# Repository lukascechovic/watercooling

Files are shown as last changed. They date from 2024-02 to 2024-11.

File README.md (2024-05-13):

# Watercooling for 3d printer based on Vz235 build and Mellow motor, drivers and extruder aluminium watercooling blocks. Warning page is under construction!

Experiences from building up watercooled 3d printer or how to make rigth choices for your build. Information based on internet "research" and communication with PC watercooling community, Alphacool and EKWB company info lines.

**Long story short** 

- one big loop
- D5/VPP655 (maybe Apex pump as cheaper D5 compatible variant)
- 2.4/4mm tubing (easy routing around printer)(polyurethane (10m) and optional silicone/pvc(2m) softer for printhead)
- 3x12cm aluminium radiator for easy top mounting (price 2eur more than 2x12 rad)
- brass nickel plated fittings (optional stainless steel 304)(idealy aluminium but I was not able to find any in this world) 
- clear coolant premix

##  Reasoning for this advice should be found next if you wanna dig deeper.

1. Mellow items for watercooling our 3D pritner https://github.com/lukascechovic/watercooling/tree/main/mellow_items
2. Fittings https://github.com/lukascechovic/watercooling/tree/main/fittings
3. Tubing https://github.com/lukascechovic/watercooling/tree/main/tubing
4. Loop topology https://github.com/lukascechovic/watercooling/tree/main/loop_topology
5. Macros to solve multiple states controlling same pin (pump and radiator fans) https://github.com/lukascechovic/watercooling/tree/main/macros
6. Stl files of pump, radiator, tubing mounts https://github.com/lukascechovic/watercooling/tree/main/cad_stl_files
7. Official statements from infolines EKWB and Alphacool https://github.com/lukascechovic/watercooling/tree/main/research%20info%20gathered

## Underline

1. **Why choose D5 pump?** It is PC watercooling industry standart. Even EKWB product video comparing D5 to other smaller DCC pump started with joke "just take D5". And yes, taking anything other than D5 is compromise. Pricewise there is nearly no difference as in smaller pump you pay for small form factor. Big one is that D5 is running at 24V so PC comunity cannot use full potential of this pump. But we can! 24V is our standart voltage :-) .

2. **Starting with budget Mellow watercooling kit?** If you dont wanna spend more than 70 euro just take Mellow watercooling kit and you will be happy and somehow youll find the way to ignore pump vibrations. But if we are building printer worth 2000 euros in items, are we wealthy enough to buy cheap things? Mellow water-cooling kit was 70 euro learning experience for me. I wish to be able skip that step.

3. **Price?**
 - 70 euro - Mellow watercooling kit
 - up to 160 euro - profi items ex. Alphacool D5-VPP655 set with reservoir, with 3x12 rad up to 160 euro (you can cut price with choosing Apex variant of the pump)

4. **Reservoir** - just take any size you like. With bigger one its easier to start loop. Our loop has around 300 ml of fluid with all possible blocks and 3x12 radiator so its no big deal even with smallest reservoir.

5. **Head pressure** - This parameter was harder one to evaluate as usually smaller pumps as DCC have bigger head pressure than D5 pumps. Head pressure is how the pump is able to overcome flow restrictions. But its also dependant from flow. If we watch only extremes from pump graphs the small DCC could seems better with higher head pressure than D5, but flow of the D5 is many times bigger than DCC with just small head pressure loss.
6.  **Coolant** - I got this answer on Alphacool forums "I'd recommend staying away from dyes just to be safe. I use Mystic Fog in my rig for the RGB effect but I accept the risk of clogs and higher maintenance involved." So if you wanna stay out of trouble just go for Clear coolant premix.

## TODO:
*add BOM

*add screws parameters

*Chatgpt please make this text readable

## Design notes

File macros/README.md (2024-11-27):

# *Temp_monitor.cfg macro turning on and off watercooling of 3d printer

## When you have watercooled extruder, drivers, motors it was neccessary to be able run watercooling for each state but with standard way you are not able to assign one pin to multiple objects.

## It is based on delayed macro which works as timer interrupt and run code which check activity and temperatures of drivers, motors, extruder, using dummy fans with fake nonused pins which can combine behaviour of controller and heater fan. 

## printer.cfg and leds.cfg to clarify pin assignement

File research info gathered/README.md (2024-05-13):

# Watercooling for 3d printers
Experiences from building up watercooled 3d printer or how to make rigth choices for your build. Information based on internet "research" and communication with PC watercooling community, Alphacool and EKWB company info lines.

*issue -1: Official statements from infolines*

**EKWB**

**Note:** Question about if EKWB D5/DDC pump can be used in aluminium loop, answer is **NO**

***Question 1:*** Hello, I would like to buy pupm from you into custom aluminium loop (alu blocks and radiators). I got confused with note in your products "This product should NOT be installed with any aluminum Fluid Gaming parts!" . Does it means I cannot use it in Aluminium containing loop? Could you please explaint to me that note and are your pumps suitable to work in custom all aluminium loop? Thanks. Have a nice day.

***Answer 1:*** Hello, thank you for contacting us. The mentioned product is not compatible with ALU parts. We used to sell products that were compatible with ALU products. Unfortunately, we no longer sell ALU products. We still have some ALU water blocks or fittings available. Unfortunately, radiators and water pumps are no longer available.

***Question 2:*** Can the 'EK-Classic Pump Reservoir 160 SPC PWM' be used in an aluminum loop?

***Answer 2:*** The EK-Classic Pump Reservoir 160 SPC PWM can be used in an aluminum loop but you will have to replace the nickel-plated brass plug with a plastic one.

**Alphacool**

***Question 1:*** Hello, I'm looking for pump into full alluminium loop. Its for custom machine with low diametter tubing (4 or 6 mm) in total length up to 10m, with 7 small aluminium blocks. If I'm not wrong I should look for higher head meters value pump. I'm searching for answers for several days but no luck for now. Last info I got is that I cannot use even stainless steel parts pump with aluminium. VPP655 pumps are marked as ceramic and plastic (Kunststoff;Keramik;) but on video they've definitely got some other metal inside. What pumps I can use in aluminium containing loop? Thanks for answer. Have a nice day.

***Answer 1:*** Hi Lukas, you can use all pump sin our assortment for full copper or aluminium loops. https://shop.alphacool.com/shop/pumpen/

***Question 2:*** "What type of metal fittings other than aluminium  can be used in full aluminium loops?  Stainless steel, brass, other?"

***Answer 2:*** Hi Lukas, thank you for getting back. Our fittings are all anodized, painted or nickel-plated and they have no contact with the liquid, so you can use any of our fittings in your loop.

***Question 3:*** "It is possible to use multiple outputs/inputs same time on the Alphacool Eisdecke Laing DDC Acryl top V.2 or Alphacool Eisdecke DDC Acryl top V.4? For example if I need to have/create two loops?"

***Answer 3:*** Hi Lukas, I am sorry but it isn´t possible to use multiple Outs on the products. **It isn´t also recommended to make a parallel loop. If you want two different loops, you will need two pumps and reservoirs.
**

**Alphacool Forums**

***Question 1:*** Hello guys,

looking for advices to optimize watercooling build for 3d printer and choose rigth components.

Setting:
-> 500wats TDP max
-> Aluminium cooling blocks on components
-> M5 and M6 threads on aluminium blocks = fittings only for 4/2.5 and 6/4 mm tubing (OD/ID) (one moving component (printihead) needs to stay on 4/2.5 tubing due to moving restrictions and weigth)
-> length of tubing max 10meters (7 components around the machine)
-> difference between highest and lowest point on machine is 0.5m
-> No hard space restrictions for radiator and pump (but more compact and visually pleasing solution is preffered)
-> prefered silent (low/no vibration operation)

Concerns:
-> choosing rigth pump for length of the loop and tubing diametters
-> choosing big enough radiator for the TDP (aluminium one due to alu blocks on components)
-> topogy of the cooling (atleast two loops ? - one for 4/2.5 tubing and one for 6/4 tubing)

So far I was thinking about:
Radiator: Alphacool ES Aluminium 360 mm T27
Fans: Yate Loon D12SH-12 with plug (2200rpm) ( 120x120x25mm )
Pump: ??
Topology: two loops

Thanks for ideas!!

PS: Some alphacool water pumps have this statement in description "Please use only in conjunction with clear transparent water cooling fluids. The particles and additives in Pastel liquids can clog and permanently damage water cooling products such as radiators, pumps, coolers and hoses.". I cant use any color premixed collants with this items or it is some special kind of colored coolants liquids and apply only for "pastels ones"?

***Answer 1:*** 1 D5 pump should be all you need unless you are doing discrete loops. If you are cooling multiple components you don't need multiple loops. Just run it in series and you'll be fine and save some money and headaches. I'd recommend staying away from dyes just to be safe. I use Mystic Fog in my rig for the RGB effect but I accept the risk of clogs and higher maintenance involved. That rad should work fine for 500 watts. Those fans should be fine also.
Edit: Just use this coolant for the best performance and longevity of the loop.

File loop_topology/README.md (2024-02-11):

# *Starting point "...just run it in series and you'll be fine and save some money and headaches."*
*PC watercooling practise*

1. You dont need high flow
2. One loop
3. Order of items in loop is not important
4. Radiator is main player in capacity of the loop to disipate heat

Explanation:

https://github.com/lukascechovic/watercooling/tree/main/research%20info%20gathered

1. You dont need high flow = lower flow = more time in radiator = lower temperature of coolant at radiator output
2. One loop = "If you are cooling multiple components you don't need multiple loops. Just run it in series and you'll be fine and save some money and headaches." I got simmilar responces from PC watercooling comunity, you can found them also beneath Vez3D videos on this topic.
3. Order of items in loop is not important = you can find lots of video on Youtube for example @Jayztwocents "Watercooling Loop Order... Does it REALLY matter?? Here's Proof" https://www.youtube.com/watch?v=RnPB_q51iVk&t=130s
4. Radiator is main player in capacity of the loop to disipate heat. And as there is a little price difference between 1x12, 2x12, 3x12 radiators. There is no good reason to not take 3x12 as futureproof choice for your build. You can have 3x12 rad from renowed brand for as little as 32 eur. Bigger radiator is easier to mount on the top of the build and also cool whole electronics.
   
   For example aluminium radiators https://shop.alphacool.com/en/shop/radiators/industrial-radiators/

*Note: My watercooling journey started on Vez3D youtube channel https://www.youtube.com/@Vez3D*

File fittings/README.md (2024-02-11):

# *Starting point*

1. aluminium cooling blocks from Mellow with M5 and M6 (driver block) threads and 4mm OD tubing
2. to preventing galvanic corrosion we should use all items with same metal as mellow blocks = aluminium

## Fittings material

***Conclusion:** my searching for full aluminium fittings failed. Closest I got were items from https://tameson.com/collections/aluminum-push-on-fittings . But upod delivery I realised that item description is false and they contain steel parts. So based on Alphacool statement we should be fine with nickel plated brass fittings with premix coolant water*

We can easily buy brass and copper nickel plated fittings and stainless steel 304 fittings, but in theory neither of those should be used together with aluminium in one cooling loop.

Here is EKWB blog on this topic with lot of details https://www.ekwb.com/blog/aluminium-vs-copper/

EKWB as main player in PC watercooling is strct about this, they are even prohibiting to use their pumps in aluminium containing loops.

On the other hand Alphacool as other player in this alows use all of their pumps in aluminium and copper loops and also using their brass nickel plated fittings in aluminium loops. (https://github.com/lukascechovic/watercooling/tree/main/research%20info%20gathered). But to be fair their statement "Our fittings are all anodized, painted or nickel-plated and they have no contact with the liquid, so you can use any of our fittings in your loop." sounds little weird to me.

EKWB picture
Galvanic_corrosion

Note to the stainless steel, in our conditions should be active if I understand it well.
active_passive_steel

## Fitting diameters

*So we have to use M5 and M6 sized fitting to fit into Mellow blocks. Inner diametter of M5 sized fitting is aproximatelly 1.8mm independent from tubing connection 2.5mm or 4mm ID. So there is questionable need for 4/6mm tubing as there is up 12 fittings with M5 screws with 1.78mm opening. To have complete info M5-4mm OD fitting have 1.66mm hole on tubing side.*

obrázok

## Fitting type
Push on compresion fittings looks like best option however even push in plastic ones, which you get with Mellow blocks, works fine for all types of tubing. Concerns with plastic ones could be heated chamber and higher temperatures.

Example of fittings:

https://www.aliexpress.com/item/1005003562742686.html?spm=a2g0o.cart.0.0.8af938davIDzIX&mp=1

https://www.aliexpress.com/item/1005001971376554.html?spm=a2g0o.cart.0.0.67b838daCjOm6Y&mp=1

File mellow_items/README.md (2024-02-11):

# *Mellow watercooling items for 3d printers

## Mellow complete basic watercooling kit

*Comment:* *Cheap and complete set, everything you need to start. Concerns are low quality controll and pump with lots of vibrations (compare to D5/DCC pumps). If you think you can somehow isolate those vibrations while pump stays on printer, you most probably dont, atleast I wasnt succesfull."

https://www.aliexpress.com/item/32888175838.html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

## Motor blocks for nema17 - included elbow fittings M5 - 4mm OD !! screws just for one length of motors

https://www.aliexpress.com/item/1005005773478512.html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,scm-url:1007.40000.327270.0,pvid:dc4a4057-3f06-441a-ac3a-f96fc6f4c963,tpp_buckets:668%232846%238115%232000&pdp_npi=4%40dis%21EUR%2136.55%2129.24%21%21%2138.47%2130.78%21%402101cff817076547497267387ee921%2112000034301466627%21rec%21SK%211841669886%21&utparam-url=scene%3ApcDetailTopMoreOtherSeller%7Cquery_from%3A

## Drivers 5160 Mellow Fly pro blocks - included M6 - 4mm OD elbow fittings

https://www.aliexpress.com/item/1005006244492970.html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,scm-url:1007.40000.327270.0,pvid:47da6230-7e59-4bf5-be31-37e7c4645041,tpp_buckets:668%232846%238115%232000&pdp_npi=4%40dis%21EUR%2161.41%2152.20%21%21%2164.63%2154.94%21%402101cff817076547551617470ee921%2112000036445101785%21rec%21SK%211841669886%21&utparam-url=scene%3ApcDetailTopMoreOtherSeller%7Cquery_from%3A

## Vz-Hextrudort-Low/WC Extruder - included M5 - 4mm OD elbow fittings

https://www.aliexpress.com/item/1005004574888848.html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

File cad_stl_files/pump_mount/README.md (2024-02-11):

# Mount for Alphacool Core 100 Aurora reservoir in bundle with pump has great value 

## https://shop.alphacool.com/en/shop/reservoirs-distro-plates/reservoir-with-pump/15483-alphacool-core-100-aurora-d5/vpp-reservoir-acetal/acrylic-with-vpp655-pwm-pump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 (there is also cheaper version https://shop.alphacool.com/en/shop/reservoirs-distro-plates/reservoir-with-pump/15380-alphacool-core-100-aurora-reservoir-acetal/acryl-with-apex-pump)

## using alphacool decoupling set with 3d printed spacers to mount into PSU https://shop.alphacool.com/en/shop/pumpen/accessories/13701-alphacool-decoupling-set-for-eheim/hydor/laing-attachment-1xig/1xag-4-pieces

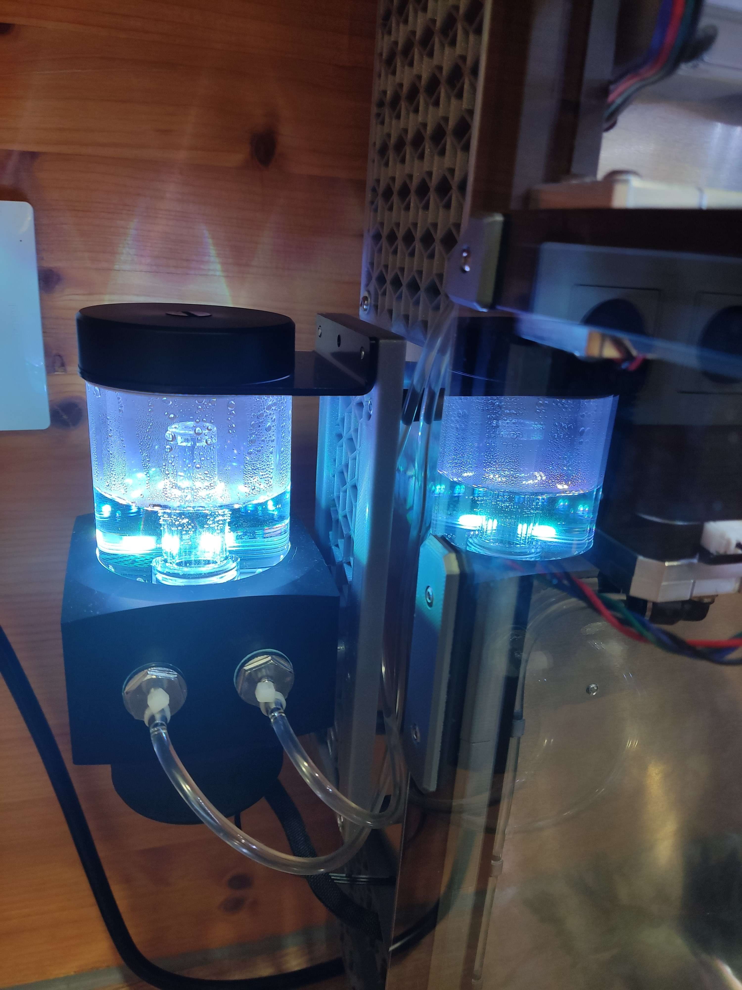
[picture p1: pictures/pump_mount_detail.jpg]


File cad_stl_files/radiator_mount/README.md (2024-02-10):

# 3x12cmm radiator top mount should work for any 3x12 radiator

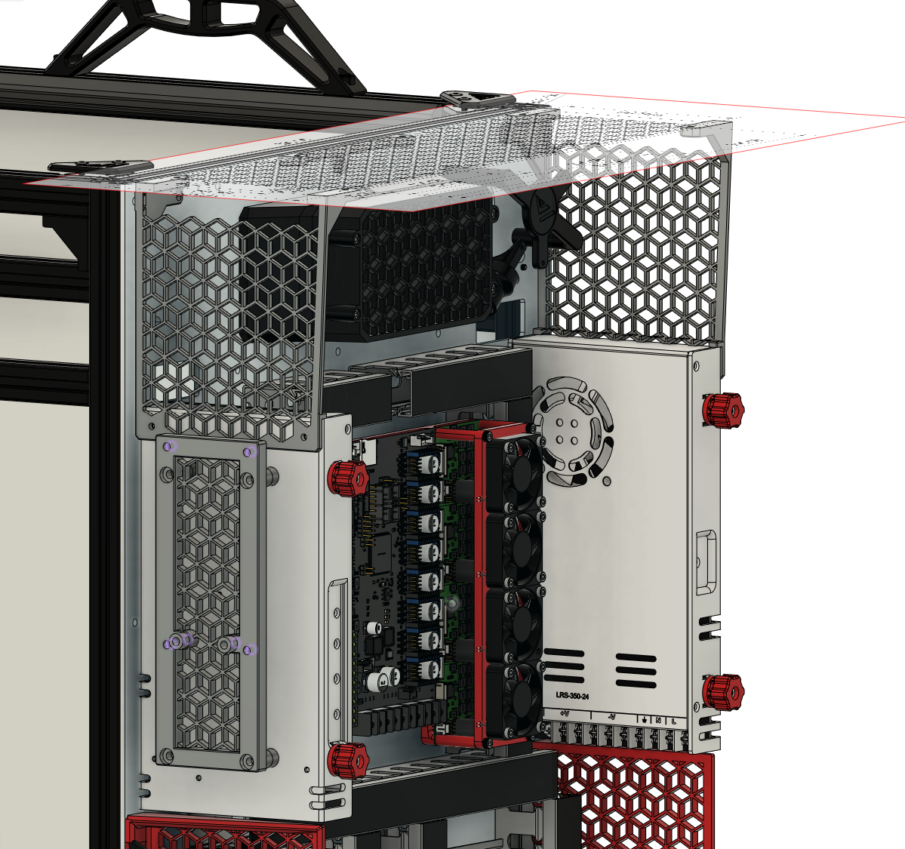
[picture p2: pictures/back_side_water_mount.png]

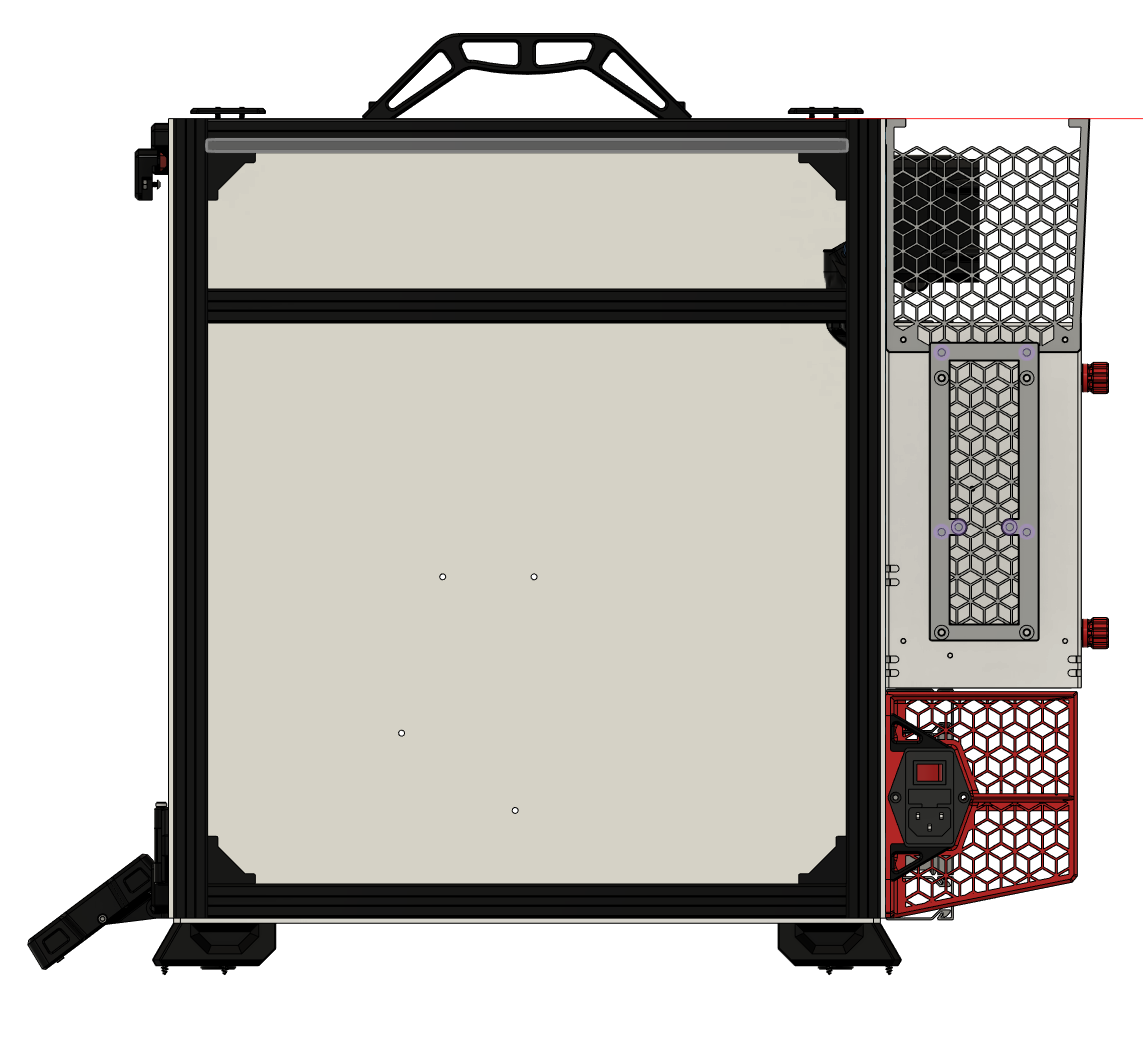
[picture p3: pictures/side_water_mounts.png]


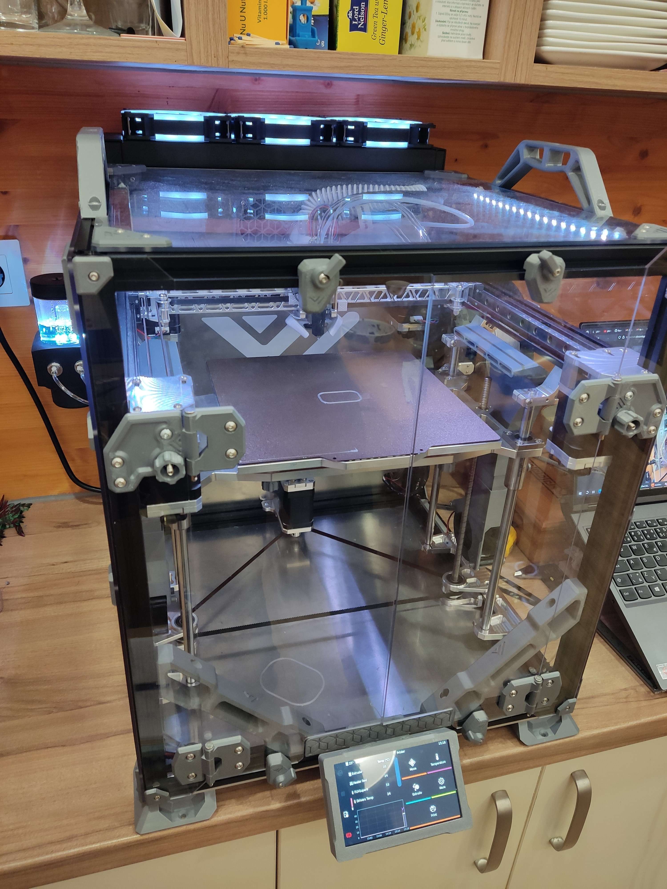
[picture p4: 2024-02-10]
pictures/front_view.jpg

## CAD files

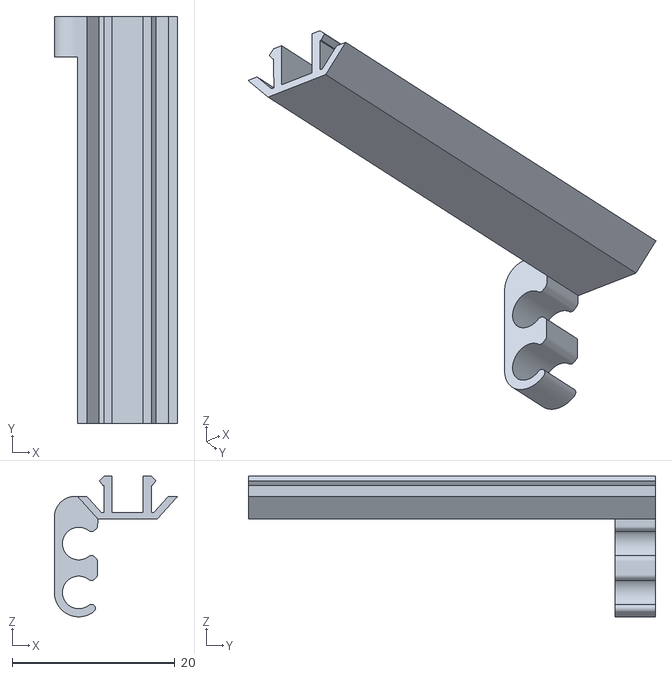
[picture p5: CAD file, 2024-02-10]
cad_stl_files/2020_cover_slot_4mm_OD_tube_guides/2020_50_front_6mm.stl
15.2 x 50.0 x 17.3

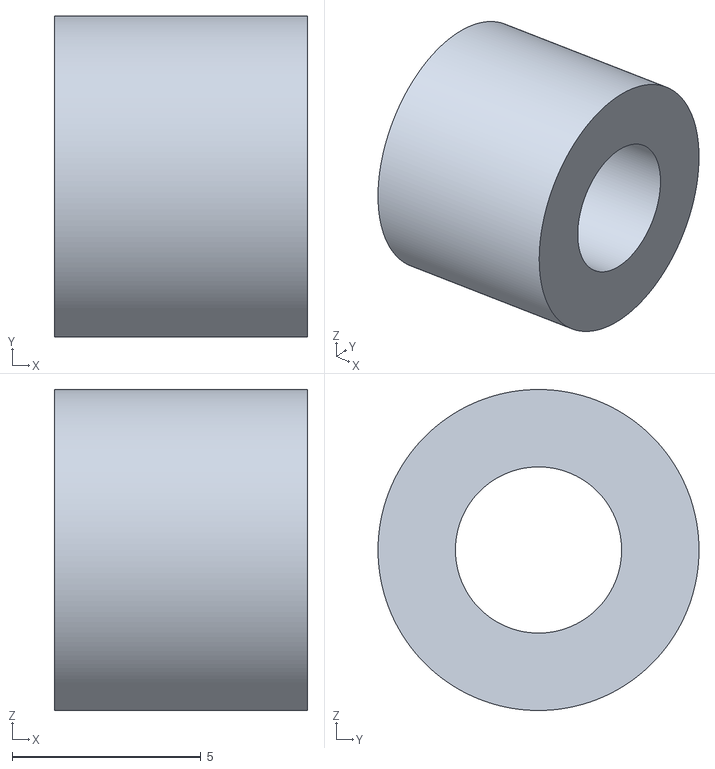
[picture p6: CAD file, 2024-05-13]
cad_stl_files/pump_mount/pump_spacer.stl
6.70 x 8.50 x 8.50

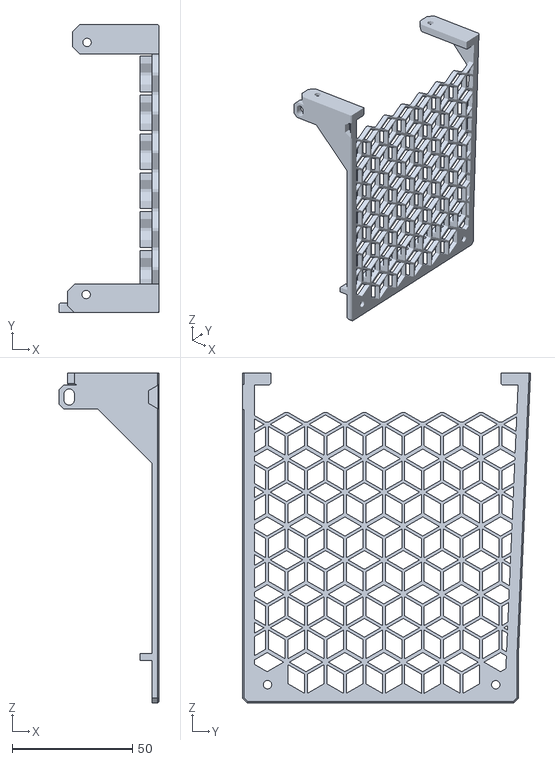
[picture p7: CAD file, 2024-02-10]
cad_stl_files/radiator_mount/side_mount.stl
41.7 x 120.0 x 137.4

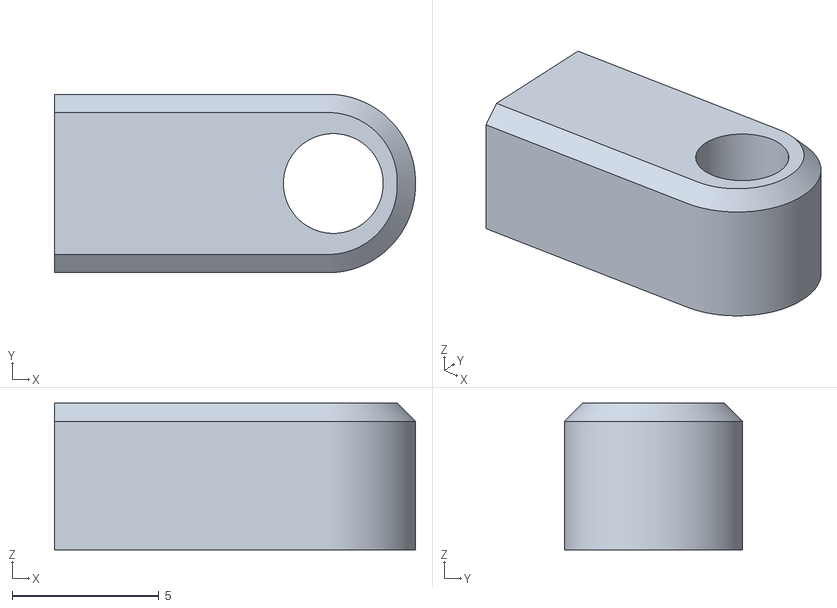
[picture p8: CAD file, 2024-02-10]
cad_stl_files/thermistor_mount/thermistor_driver_mellow_block.stl
12.3 x 6.08 x 5.00

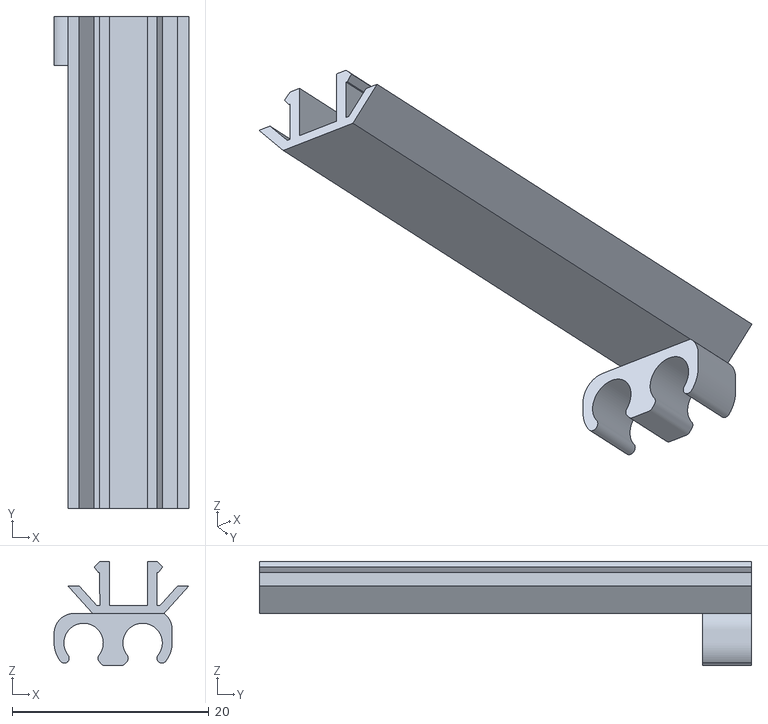
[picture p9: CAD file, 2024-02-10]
cad_stl_files/2020_cover_slot_4mm_OD_tube_guides/2020_50_back_6mm.stl
13.7 x 50.0 x 10.6

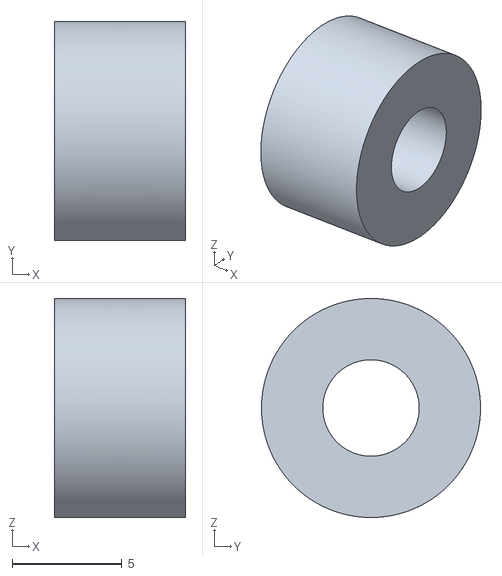
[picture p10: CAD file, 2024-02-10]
cad_stl_files/pump_mount/reservoir_PSU_mount_spacer_vibration.stl
6.00 x 10.0 x 10.0

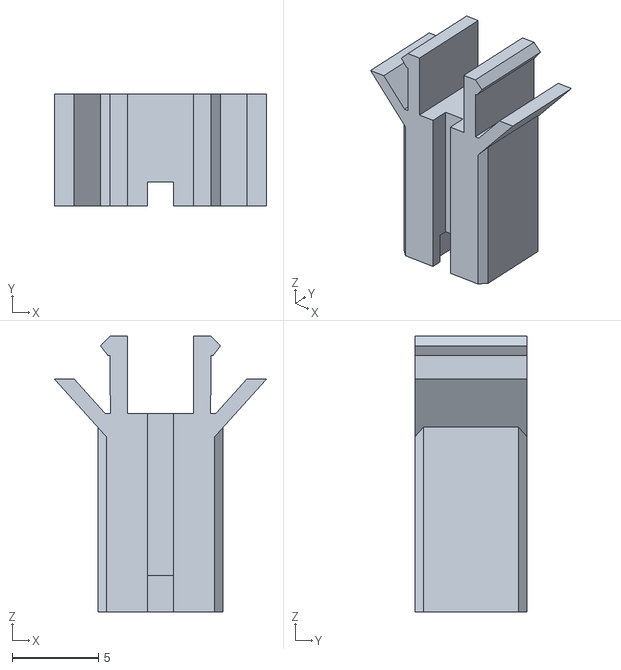
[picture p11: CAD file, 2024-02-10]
cad_stl_files/thermistor_mount/2020_motor_therm_mount_135.stl
12.3 x 6.50 x 16.0

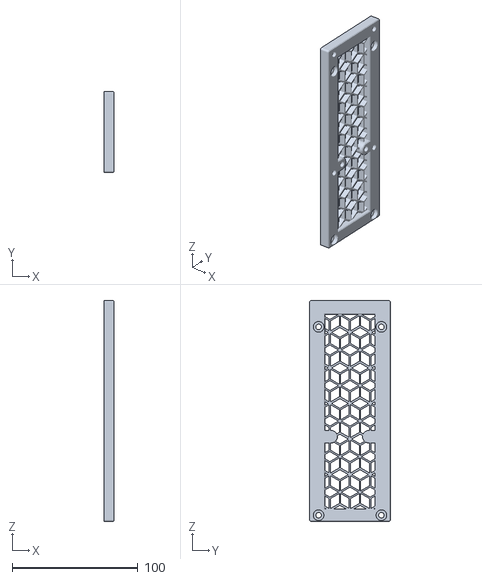
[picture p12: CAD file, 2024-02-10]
cad_stl_files/pump_mount/reservoir_PSU_mount.stl
8.00 x 64.5 x 176.0

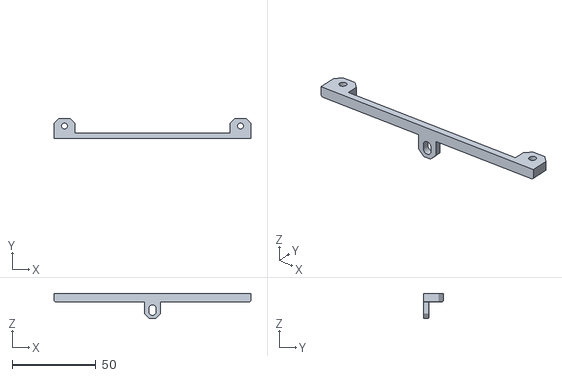
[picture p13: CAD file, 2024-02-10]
cad_stl_files/radiator_mount/mid_mount.stl
117.5 x 12.0 x 15.0

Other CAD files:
cad_stl_files/radiator_mount/side_mount_rigth.stl

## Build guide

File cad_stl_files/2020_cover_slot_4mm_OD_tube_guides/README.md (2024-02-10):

# Guiding for 4mm OD tubing using 2020 alu profiles, with posiibility to guide cables underneath

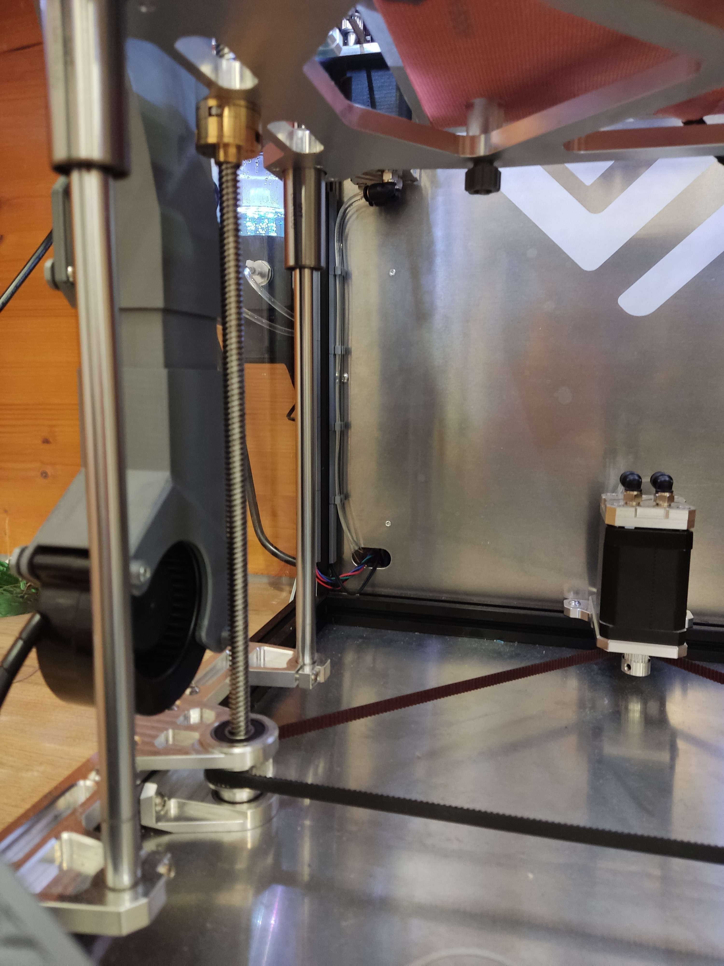
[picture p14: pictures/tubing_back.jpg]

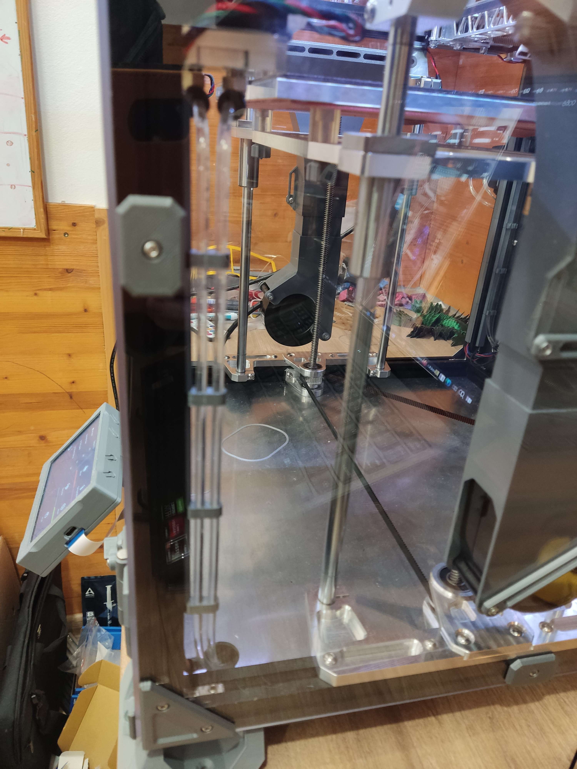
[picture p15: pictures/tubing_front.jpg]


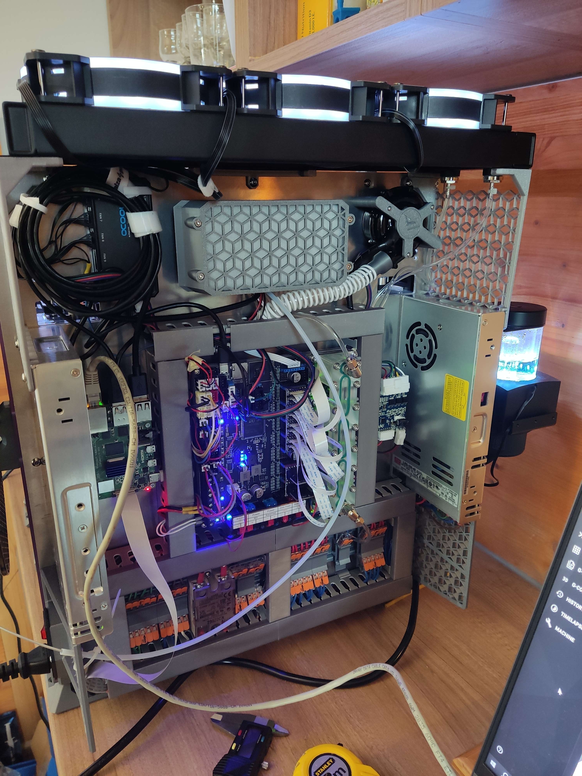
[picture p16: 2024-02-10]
pictures/printer_back.jpg

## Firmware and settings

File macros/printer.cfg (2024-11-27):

### For Fly Super 8 V1.3 ####
### And Mellow Kit  ####
### For Fly Super pro 8, the SPI bus is spi1A
### For Fly Super 8 V1.3, the SPI bus is spi3

[include mainsail.cfg]
[include timelapse.cfg]
[include Exclude_Object.cfg]
[include Start_Stop.cfg]
[include Macro.cfg]
[include Speed.cfg]
[include K-ShakeTune/*.cfg]
[include temp_monitor.cfg]
[include leds.cfg]
[include led_progress.cfg]
[display_status]
[exclude_object]
#[virtual_sdcard]
#path: ~/printer_data/gcodes
[pause_resume]
recover_velocity: 350

# Enable arcs support for Orcaslicer.
[gcode_arcs]
resolution: 0.1

[gcode_macro _CLIENT_VARIABLE]
variable_use_custom_pos   : True  # use custom park coordinates for x,y [True/False]
variable_custom_park_x    : 117.0   # custom x position; value must be within your defined min and max of X
variable_custom_park_y    : 2.0   # custom y position; value must be within your defined min and max of Y
#variable_custom_park_dz   : 2.0   # custom dz value; the value in mm to lift the nozzle when move to park position
#variable_user_resume_macro: "FANS_OFF"    # Everything inside the "" will be executed before the klipper base resume (RESUME_BASE) function
#variable_user_pause_macro : "FANS_OFF"    # Everything inside the "" will be executed after the klipper base pause (PAUSE_BASE) function
#variable_user_cancel_macro: "SET_FAN_SPEED FAN=fan0 SPEED=0"    # Everything inside the "" will be executed before the klipper base cancel (CANCEL_PRINT_BASE) function
gcode:

[beacon]
serial: /dev/serial/by-id/usb-Beacon_Beacon_RevH_71E91D854E5737374D202020FF102937-if00
x_offset: 0 # update with offset from nozzle on your machine
y_offset: 27.065 # update with offset from nozzle on your machine
mesh_main_direction: x
mesh_runs: 2

[safe_z_home]
home_xy_position: 117.5, 117.5 # update for your machine
z_hop: 3

[bed_mesh]
algorithm: bicubic
speed: 400
mesh_min: 15, 30
mesh_max: 215, 215
probe_count: 30, 30

##### VzBoT############
#######################
[input_shaper]
shaper_freq_x: 149.8
shaper_type_x: mzv
shaper_freq_y: 85.6
shaper_type_y: mzv

[printer]
kinematics: corexy
max_velocity: 1000  #2500
max_accel: 40000
max_accel_to_decel: 40000
max_z_velocity: 20
max_z_accel: 1500
square_corner_velocity: 10

########################
########################


[mcu]
serial: /dev/serial/by-id/usb-Klipper_stm32h723xx_23003E000451323336333538-if00  # put your own Serial here.
#restart_method: command

[temperature_sensor FLY-Super8]
sensor_type: temperature_mcu

[mcu rpi]
serial: /tmp/klipper_host_mcu

#[adxl345]
#cs_pin: rpi:None
#axes_map: -y,-x,-z #left side   #x,y,-z #front

[resonance_tester]
#accel_chip: adxl345
accel_chip: beacon
probe_points:
    117.5, 117.5, 20  # an example

[temperature_sensor raspberry_pi]
sensor_type: temperature_host
min_temp: 10
max_temp: 100

########################
########################

[stepper_x]
##	in M6 position
step_pin: PE0
dir_pin: PG3
enable_pin: !PG4
rotation_distance: 40
microsteps: 16
full_steps_per_rotation: 200  
endstop_pin: PG12            #make sure to set the correct pin here.
position_endstop: 0
position_min: 0
position_max: 235
homing_speed: 50 
homing_retract_dist: 0

[tmc5160 stepper_x] 
#spi_bus: spi3
cs_pin: PG2
#diag_pin: PA8
interpolate: false
run_current: 1.9  #1.9
sense_resistor: 0.033
spi_software_mosi_pin: PB5
spi_software_miso_pin: PB4
spi_software_sclk_pin: PB3
#driver_SGT: -64 # -64 is most sensitive value, 63 is least sensitive
driver_TBL: 1
driver_TOFF: 3
driver_DISS2G: 1
driver_DISS2VS: 1


[stepper_x1]
##	in M5 position
step_pin: PE1
dir_pin: PF0
enable_pin: !PC15
rotation_distance: 40
microsteps: 16
full_steps_per_rotation: 200
#endstop_pin: tmc5160_stepper_x:virtual_endstop 

[tmc5160 stepper_x1] 
#spi_bus: spi3
cs_pin: PF1
#diag_pin: PD6
interpolate: false
run_current: 1.9 #1.9
sense_resistor: 0.033
spi_software_mosi_pin: PB5
spi_software_miso_pin: PB4
spi_software_sclk_pin: PB3
#driver_SGT: -64 # -64 is most sensitive value, 63 is least sensitive
driver_TBL: 1
driver_TOFF: 3
driver_DISS2G: 1
driver_DISS2VS: 1


[stepper_y]
##	in M4 position
step_pin: PE15
dir_pin: PE11
enable_pin: !PF2
rotation_distance: 40
microsteps: 16
full_steps_per_rotation: 200  
endstop_pin: PG11                 #make sure to set the correct pin here.
position_endstop: -0
position_min: 0
position_max: 235
homing_speed: 50  
homing_retract_dist: 0

[tmc5160 stepper_y] 
#spi_bus: spi3
cs_pin: PE10
#diag_pin: PD7
interpolate: false
run_current: 1.9 #1.9
sense_resistor: 0.033
spi_software_mosi_pin: PB5
spi_software_miso_pin: PB4
spi_software_sclk_pin: PB3
#driver_SGT: -64 # -64 is most sensitive value, 63 is least sensitive
driver_TBL: 1
driver_TOFF: 3
driver_DISS2G: 1
driver_DISS2VS: 1

[stepper_y1]
##	in M3 position
step_pin: PE14
dir_pin: PE8
enable_pin: !PE9
rotation_distance: 40
microsteps: 16
full_steps_per_rotation: 200
#endstop_pin: tmc5160_stepper_y:virtual_endstop  

[tmc5160 stepper_y1] 
#spi_bus: spi3
cs_pin: PE7
#diag_pin: PG9
interpolate: false
run_current: 1.9 #1.9
sense_resistor: 0.033
spi_software_mosi_pin: PB5
spi_software_miso_pin: PB4
spi_software_sclk_pin: PB3
#driver_SGT: -64 # -64 is most sensitive value, 63 is least sensitive
driver_TBL: 1
driver_TOFF: 3
driver_DISS2G: 1
driver_DISS2VS: 1

#########################

[stepper_z]
## In M1 position
step_pin: PE3
dir_pin: PF13
enable_pin: !PF14
microsteps: 32
rotation_distance: 4
##Beacon conditional disable
#endstop_pin: PG10            #make sure to set the correct pin here.
#position_endstop: 0.0
position_min: -0.1
position_max: 219
full_steps_per_rotation: 200
homing_retract_dist: 5.0
homing_positive_dir: false
homing_speed: 5.0
second_homing_speed: 2.5
##beacon
endstop_pin: probe:z_virtual_endstop # use beacon as virtual endstop
homing_retract_dist: 0 # beacon needs this to be set to 0
[tmc2209 stepper_z]
interpolate: false
uart_pin: PF12
run_current: 1.2
stealthchop_threshold: 0

[extruder]
## In M0 position
### Vz-HextrudORT
step_pin: PE2
dir_pin: PC5
enable_pin: !PF11
microsteps: 16
#Alu VZhextrudort Moons 8T
#rotation_distance: 22.2
#Gear_ratio: 50:8
#Alu VZhextrudort Moons 10T
rotation_distance: 22.59 #22 
gear_ratio: 50:10 
#VZHextrudort LDO 20mm
#rotation_distance: 4.71
nozzle_diameter: 0.5
filament_diameter: 1.750

heater_pin: PB0
sensor_type: PT1000
sensor_pin: PF4

#control: pid
#pid_Kp=28.737 
#pid_Ki=1.935 
#pid_Kd=106.684
min_temp: 0
max_temp: 350
full_steps_per_rotation: 200
max_extrude_only_distance: 1000.0
max_extrude_cross_section: 500
max_extrude_only_velocity: 200
max_extrude_only_accel: 10000
min_extrude_temp: 0
pressure_advance: 0.025
pressure_advance_smooth_time: 0.03

[tmc2209 extruder]
uart_pin: PC4
interpolate: false
run_current: 0.7
sense_resistor: 0.110

########################
########################

[heater_bed]
heater_pin: PE5
sensor_type: NTC 100K MGB18-104F39050L32
pullup_resistor: 4700
#sensor_type: Generic 3950
sensor_pin: PC1
#control: pid
#pid_Kp: 66.746
#pid_Ki: 3.504
#pid_Kd: 317.878
min_temp: 0
max_temp: 130 #130 default


########################
#### FANS ##############
########################

[fan_generic fan0] #[fan] #
##	Print Cooling Fan - PF8
pin: PF8 #turbo
max_power: 1
cycle_time: 0.002
hardware_pwm: false
shutdown_speed: 0
off_below: 0.12

#[heater_fan hotend_fan]
###	Hotend Fan - FAN0 Connector
### in case of a watercooler that is 24V use a Heater Pin like PF7 Heat3 for a larger mosfet that can handle more amps.
#pin: PA3 #cerpadlo
#max_power: 1
#kick_start_time: 0.5
#heater: extruder
#heater_temp: 50.0

#[fan_generic Exhaust_fan]
##  exhaust fan - In FAN4
#pin: PA15
#max_power: 1
#shutdown_speed: 0
#kick_start_time: 0.1
#off_below: 0.10

#[fan_generic chamber_fan]
###  chamber fan - In FAN9 Positon
#pin: PD15
#max_power: 1
#shutdown_speed: 0
#kick_start_time: 0.1
#off_below: 0.10

[multi_pin static_multi_pin]
pins: PA0, PA1
#   A comma separated list of pins associated with this alias. This
#   parameter must be provided

[fan_generic fan2]
##  RSCS Fans - In FAN1 Positon
pin = multi_pin:static_multi_pin
max_power: 1
shutdown_speed: 0
kick_start_time: 0.1
off_below: 0.06

[multi_pin filtration_multi_pin]
pins: PB10, PD12
#   A comma separated list of pins associated with this alias. This
#   parameter must be provided

[fan_generic fan3]
##  RSCS Fans - In FAN1 Positon
pin = multi_pin:filtration_multi_pin
max_power: 1
shutdown_speed: 0
kick_start_time: 0.1
off_below: 0.06

[gcode_macro M106]
gcode:
    {% set fan = 'fan' + (params.P|int if params.P is defined else 0)|string %}
    {% set speed = (params.S|float / 255 if params.S is defined else 1.0) %}
    SET_FAN_SPEED FAN={fan} SPEED={speed}

[gcode_macro FANS_OFF]
gcode:
  SET_FAN_SPEED FAN=fan0 SPEED=0
  SET_FAN_SPEED FAN=fan2 SPEED=0
  SET_FAN_SPEED FAN=fan3 SPEED=0
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

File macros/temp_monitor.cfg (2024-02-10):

# Monitoring loop. Begins at Klipper start.
# todo tune naming of variables and macros, comments
[delayed_gcode CHECK_ALL_FANS]
initial_duration: 5 #without this delay there is chance to end in error / hypothesis
gcode:
    TEMPS_CHECK
    UPDATE_DELAYED_GCODE ID=CHECK_ALL_FANS DURATION=10

[gcode_macro TEMPS_CHECK]
variable_active: 0
gcode:
    #{% set head_temp_on = 50|float %} #handled in dummy_hotend_fan
    #{% set temp_head = printer[printer.toolhead.extruder].temperature|float %} #handled in dummy_hotend_fan
    {% set drivers_temp_on = 33|float %} #max drivers temperature by HALT handled in [temperature_sensor drivers_temp] later rework to pause??
    {% set drivers_temp_off = 28|float %} ##hysteresis for driver temps
    {% set temp_drivers = printer['temperature_sensor drivers_temp'].temperature|float %}
    {% set fan_controller_speed = printer['controller_fan dummy_motors_fan'].speed|float  %}
    {% set fan_hotend_speed = printer['heater_fan dummy_hotend_fan'].speed|float  %}

    #debug print into console
    #{action_respond_info("Active cnt: %.1f, Drivers Temp: %.1f, Fan_controller: %.1f, Fan_hotend: %.1f" % (active, temp_drivers, fan_controller_speed, fan_hotend_speed))}

    {% if ((temp_drivers >= drivers_temp_on) or (fan_controller_speed>0) or (fan_hotend_speed>0)) and (active==0) %}
        SET_GCODE_VARIABLE MACRO=TEMPS_CHECK VARIABLE=active VALUE=1
        WATER_COOLING_ON
    {% elif (temp_drivers <= drivers_temp_off) and (fan_controller_speed==0) and (fan_hotend_speed==0) and (active==1) %} #hysteresis for driver temps     
        SET_GCODE_VARIABLE MACRO=TEMPS_CHECK VARIABLE=active VALUE=0
        WATER_COOLING_OFF
    {% else %}
    #M118 Nothing from above #debug 
    {% endif %}
      
[gcode_macro WATER_COOLING_ON]
gcode:
  SET_FAN_SPEED FAN=water_pump SPEED=0.52
  SET_FAN_SPEED FAN=radiator_fan SPEED=1
  M118 START Watercooling                  #debug print
  
[gcode_macro WATER_COOLING_OFF]
gcode:
  SET_FAN_SPEED FAN=water_pump SPEED=0
  SET_FAN_SPEED FAN=radiator_fan SPEED=0
  M118 END Watercooling                    #debug print

[fan_generic water_pump] 
# This is if you connect your driver fan to Super8 
#or if you want to add fan to the Super8. Other wise connect them in the driver fan ports
#stepper: stepper_x
#stepper: stepper_x1
#stepper: stepper_y
#stepper: stepper_y1
#heater: extruder
pin: PB1
max_power: 0.6
shutdown_speed: 0
kick_start_time: 0.5
off_below: 0.45 #for 0.6 max power
#idle_timeout: 60
#fan_speed: 0.4
#tachometer_pin: PF10  #^PG9
#tachometer_ppr: 2

[fan_generic radiator_fan]
##  RSCS Fans - In FAN1 Positon
pin: PD14
#cycle_time: 0.001
#hardware_pwm: false
max_power: 1
shutdown_speed: 0
kick_start_time: 0.1
#off_below: 0.6

[controller_fan dummy_motors_fan]
##  radiator fans
pin: PD6
#heater: extruder
heater: heater_bed
stepper: stepper_x
stepper: stepper_x1
stepper: stepper_y
stepper: stepper_y1
#cycle_time: 0.001
#hardware_pwm: false
max_power: 1
shutdown_speed: 0
kick_start_time: 0.5
idle_timeout: 0
#off_below: 0.6

[heater_fan dummy_hotend_fan]
###	Hotend Fan - FAN0 Connector
### in case of a watercooler that is 24V use a Heater Pin like PF7 Heat3 for a larger mosfet that can handle more amps.
pin: PA8 #pump
max_power: 1
kick_start_time: 0.5
heater: extruder
heater_temp: 50.0

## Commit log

2024-02-10 add
    add
    [2020_50_back_6mm.stl, 2020_50_front_6mm.stl, 2020_motor_therm_mount_135.stl]
2024-04-23 research: include information EK-Classic Pump Reservoir 160 SPC PWM
    I had one of these not being used and checked with EKWB if it can be used
    in aluminum loops since its documentation doesn't specify what kind of loops
    it can be used.
2024-11-27 additional macro files to clarify setting and pin assignement
    [leds.cfg, printer.cfg]
